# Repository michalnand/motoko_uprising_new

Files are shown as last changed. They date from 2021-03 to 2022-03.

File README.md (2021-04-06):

# motoko uprising new
motoko uprising line following robot,

**highlights**
- cpu stm32f7, 216MHz ARM Cortex M7
- DRV8834, TI motor driver
- 8x phototransistor + white led as line sensor
- IR leds for obstacle detection
- 2x pololu motors HP, 1:30 with encoder
- expansion : camera, laser sensor

- custom operating system
- reccurent LSTM in controll loop
- total 3 other PIDs used

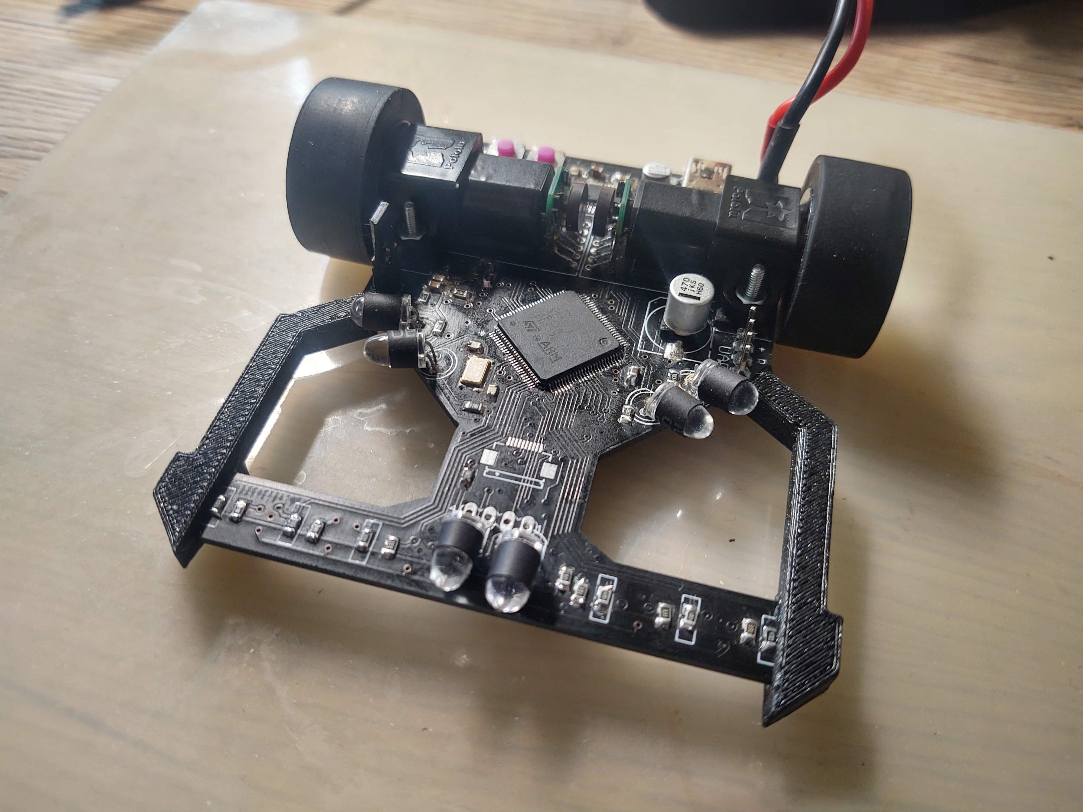
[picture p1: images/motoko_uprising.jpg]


# structure
 
 * src
    * firmware - robot main firmware
    * robot_debug_py - debug application
    * AI gym env for reinforcement learning [gym-line_follower](src/gym-line_follower/)
    * TODO rl_line_follower [rl_line_follower](src/rl_line_follower/)

* hardware 
    * eagle files [hardware](hardware/)
    * gerber outputs [files](hardware/CAMOutputs/)
    * stl for 3D printed parts [files](hardware/mechanical/)

# supervised learning for line position prediction

**key points**
* **input**  is time series sequence from 8 line sensors
* **output** is classification into three classes (left, straight, righ)
* RNN GRU with 64 units used, and linear layer with 3 neurons

* confusion matrix result for **float32**
```bash
accuracy   = 89.037 [%]
hit_count  = 116703
miss_count = 14369

class_accuracy = 90.952%   90.474%   84.811%   

confusion_matrix = 
       28326        1376           8
        2817       57907        5448
           0        4720       30470
```

* confusion matrix result for **int8** quantization

```bash
testing result
accuracy   = 87.792 [%]
hit_count  = 115071
miss_count = 16001

class_accuracy = 79.176%   91.345%   87.918%   

confusion_matrix = 
       22858        3566           0
        6011       62800        4041
           0        2383       29413
```

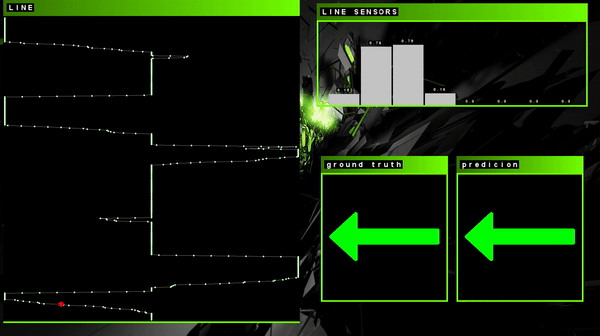
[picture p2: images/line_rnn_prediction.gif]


# reinforcement learning in Pybullet ENV

**key points**
* **state** is 256 last line positions, motors velocities, and line present flag

* PPO algorithm for continuous action space

* GRU model with three output heads (mean, variance, value)

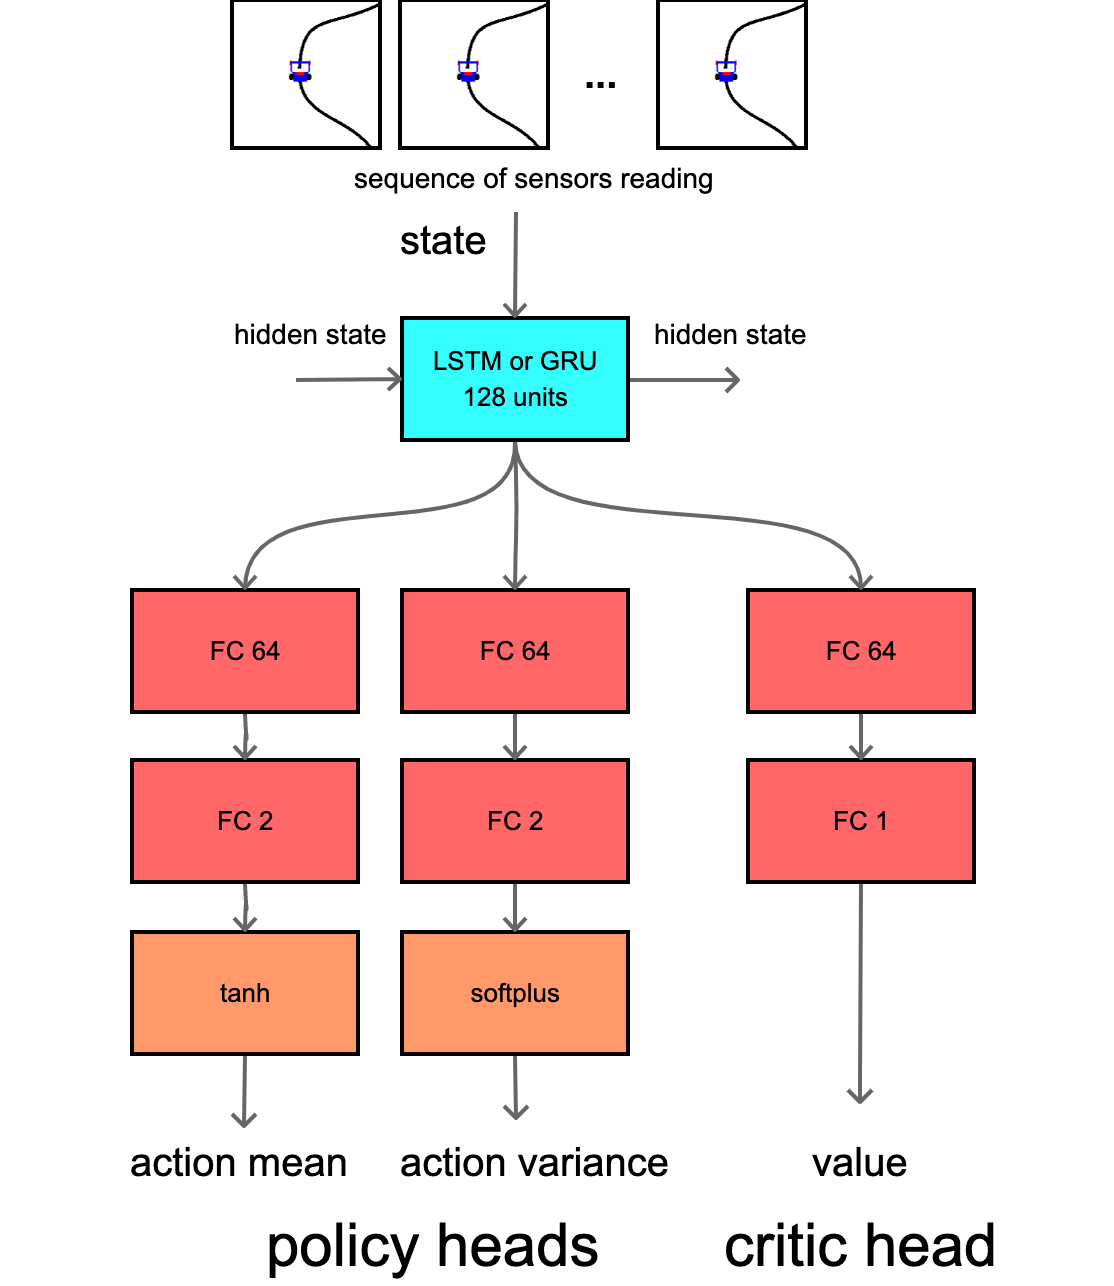
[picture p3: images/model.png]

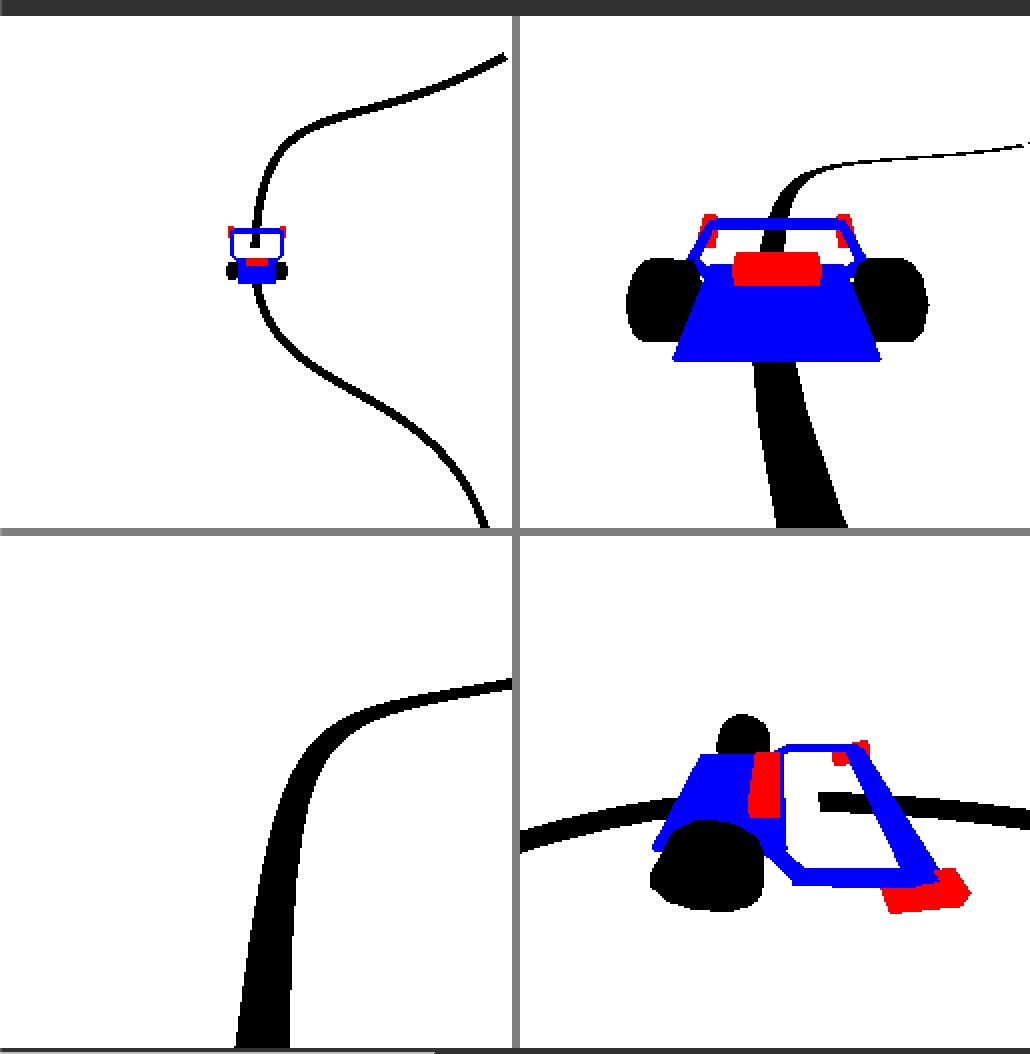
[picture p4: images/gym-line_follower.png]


# hardware

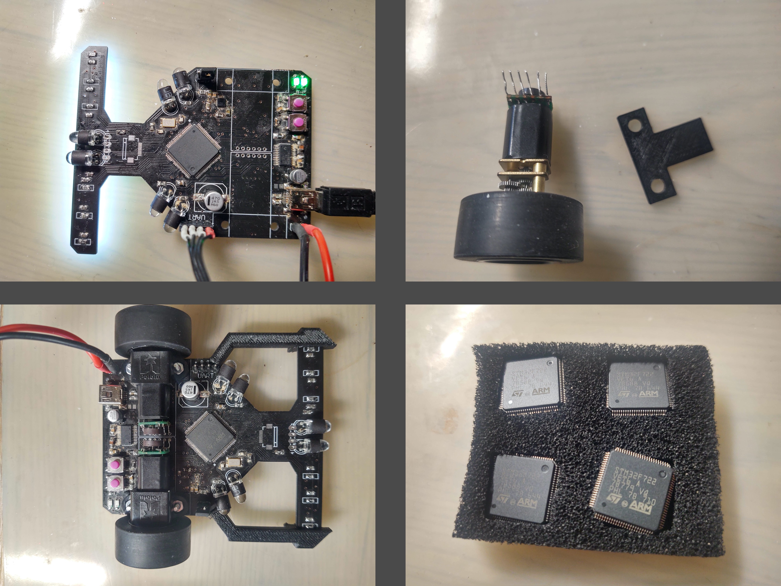
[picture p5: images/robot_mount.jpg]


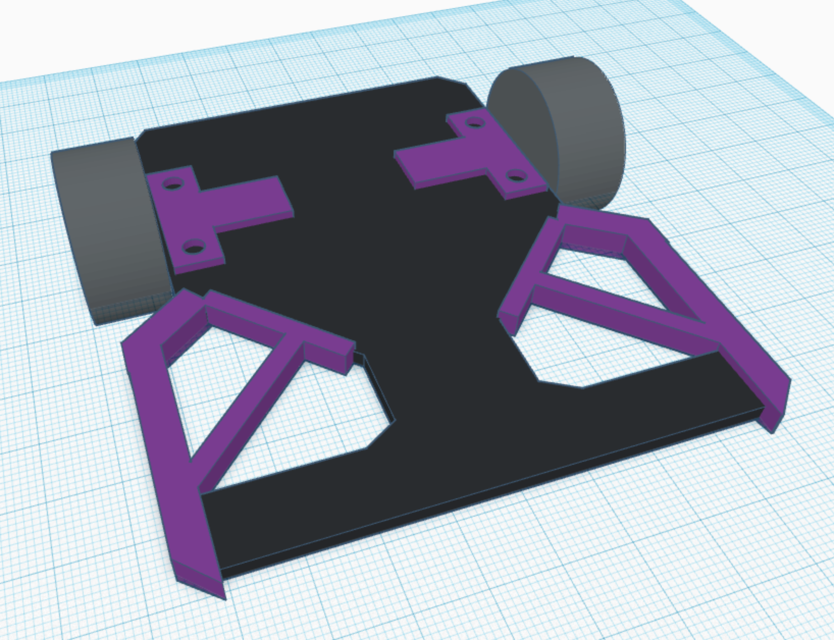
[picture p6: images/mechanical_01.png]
mechanical

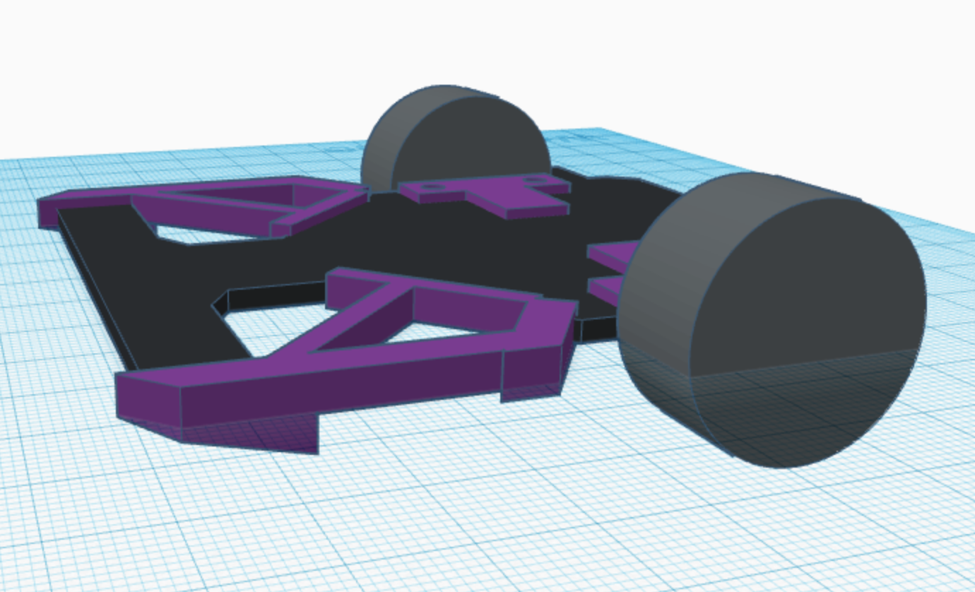
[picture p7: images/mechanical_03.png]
mechanical


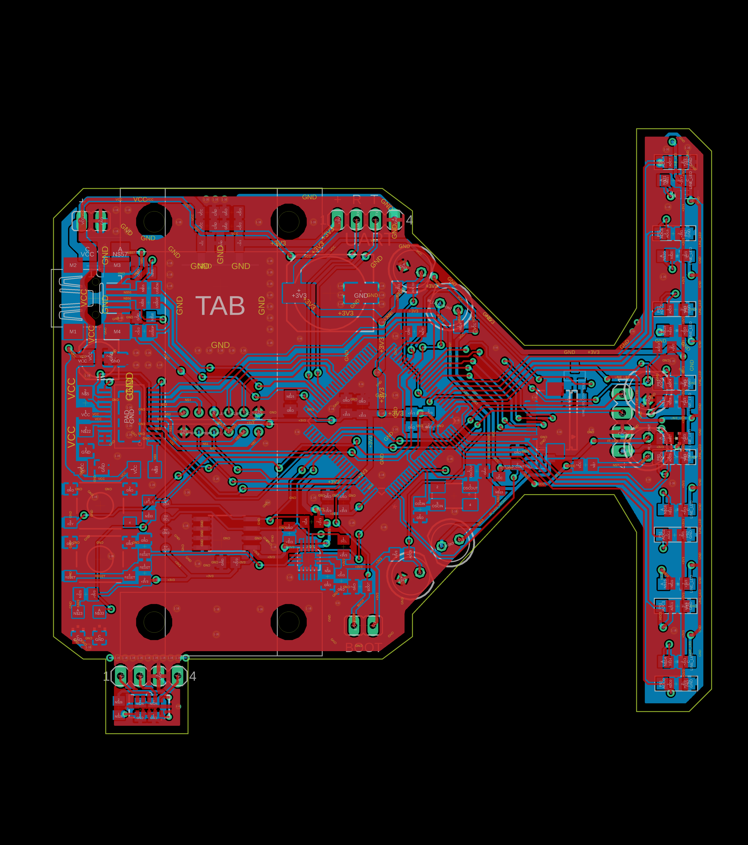
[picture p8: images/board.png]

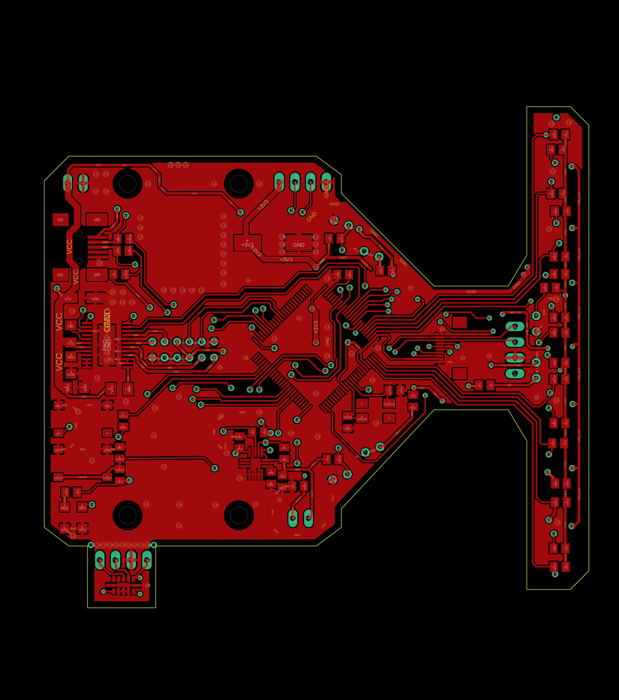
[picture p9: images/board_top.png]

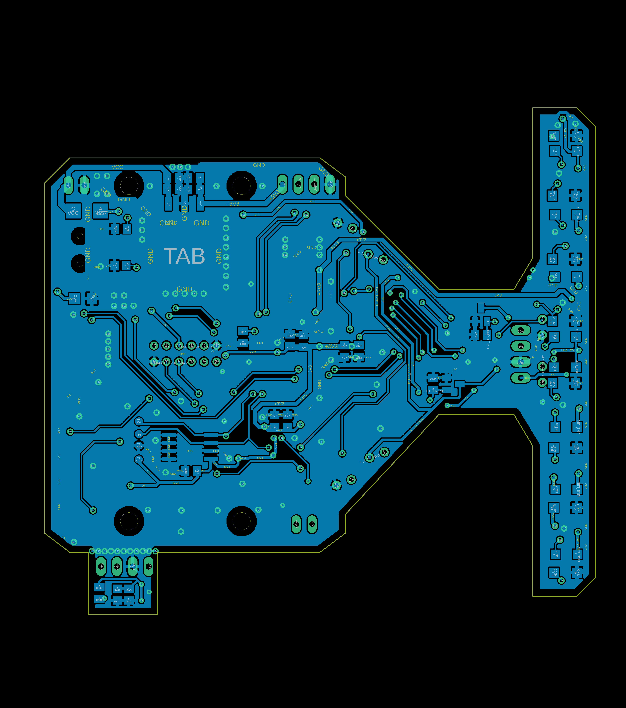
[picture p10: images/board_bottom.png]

hardware

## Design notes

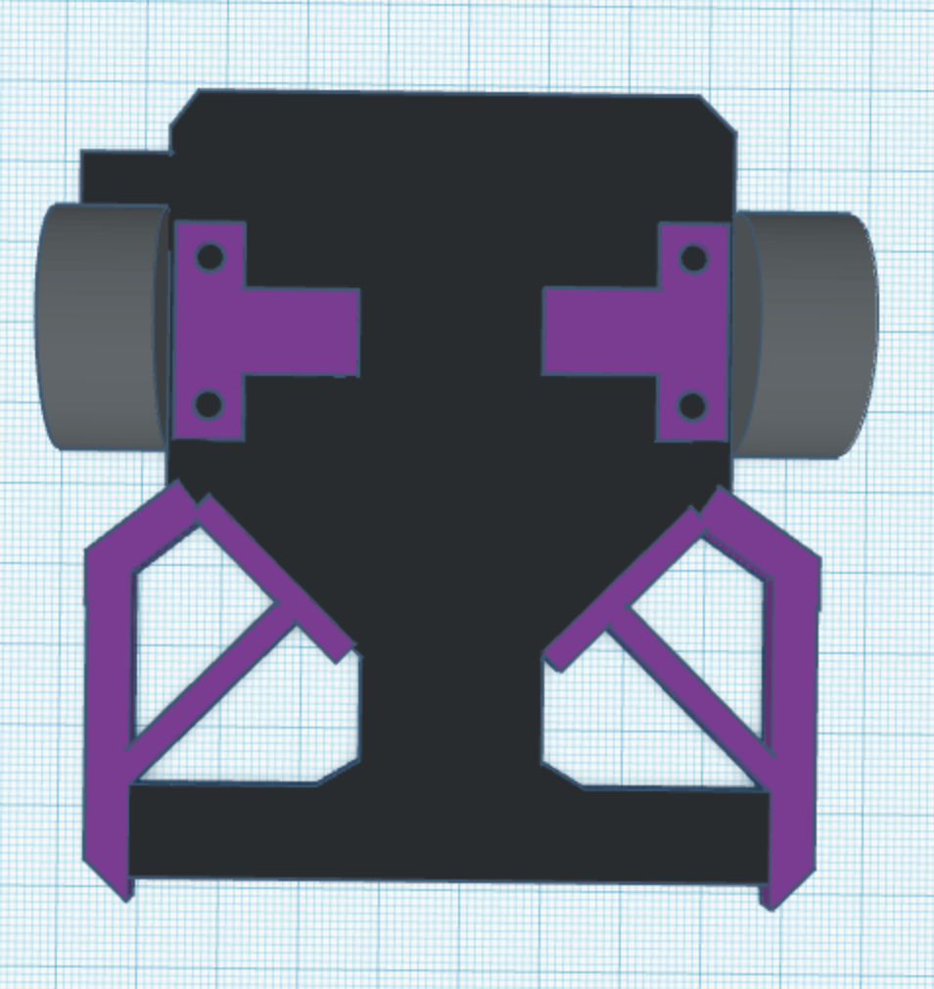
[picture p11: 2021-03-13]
images/mechanical_02.png

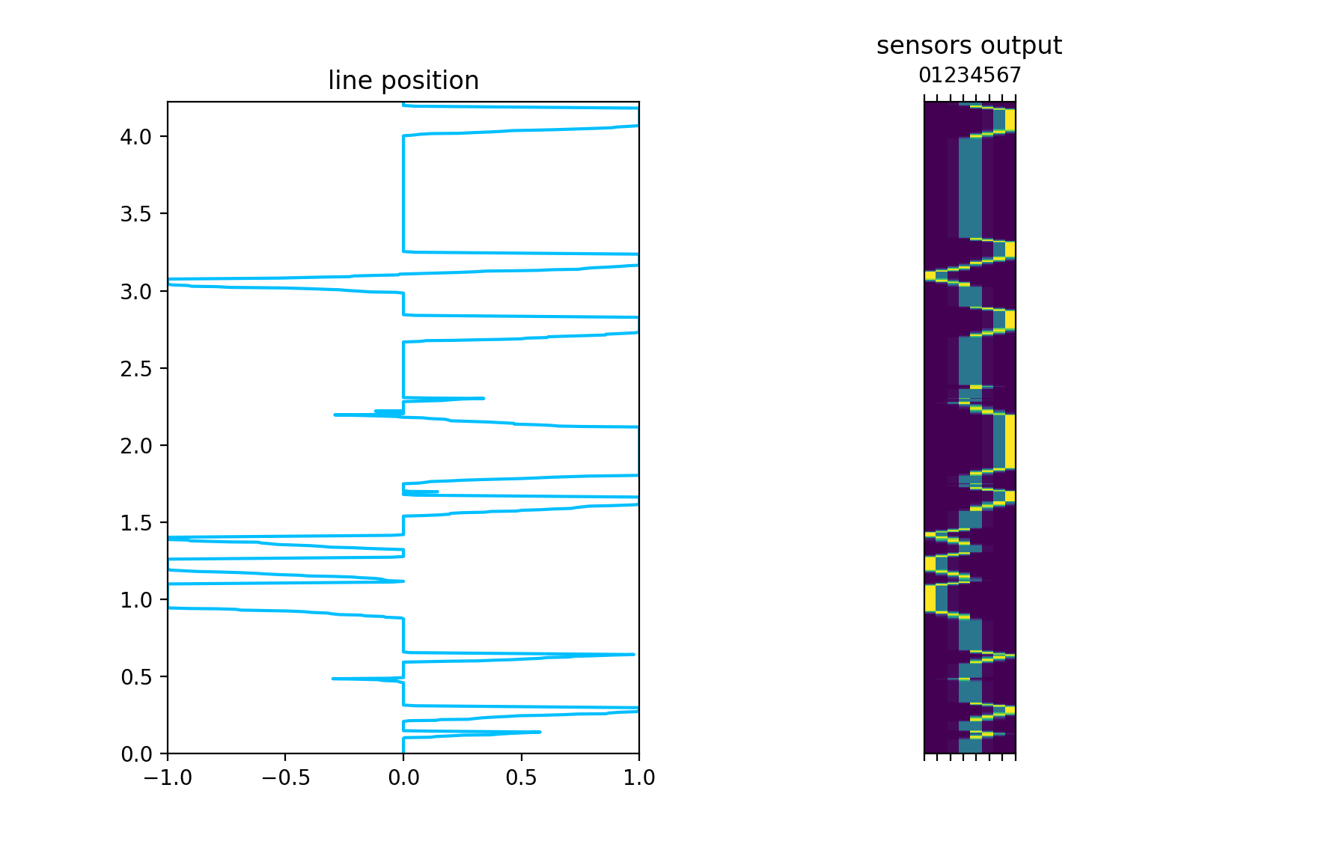
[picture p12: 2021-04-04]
images/line_follower_dataset.png

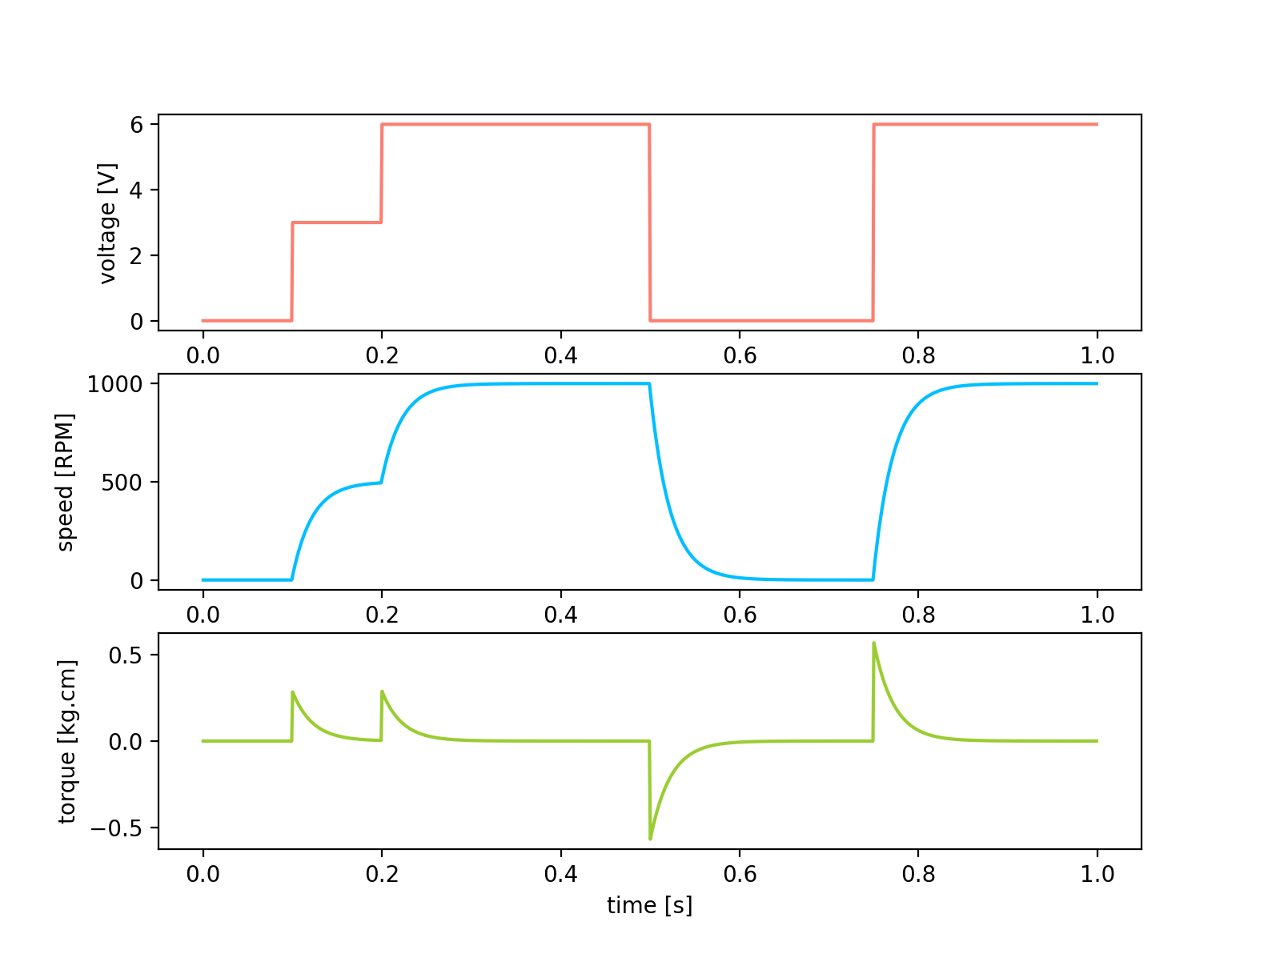
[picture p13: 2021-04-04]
images/motor_model.png

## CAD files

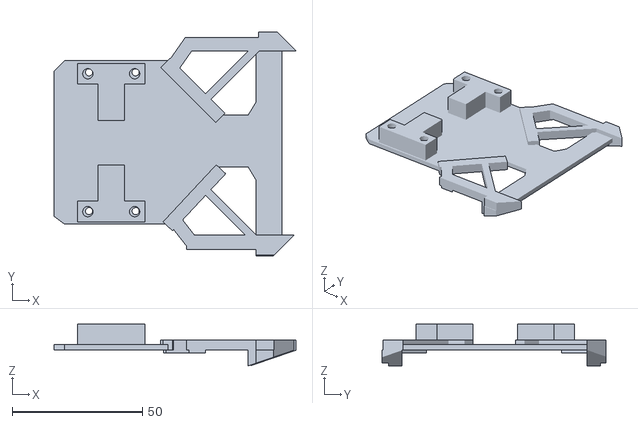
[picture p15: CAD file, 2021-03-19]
hardware/mechanical/model.stl
93.0 x 86.0 x 16.0

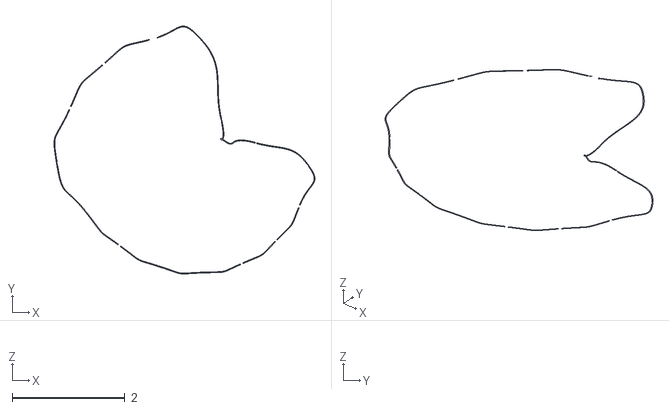
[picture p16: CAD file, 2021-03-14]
src/gym-line_follower/gym_line_follower/envs/models/lines/55.obj
4.62 x 4.39 x 0

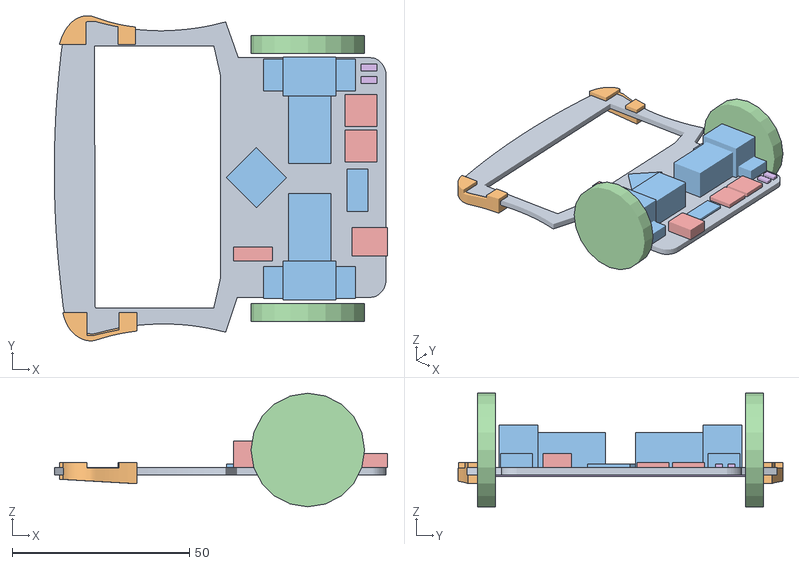
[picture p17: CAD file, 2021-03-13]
src/robot_debug_py/resources/robot_model/model.obj
93.9 x 91.6 x 32.0

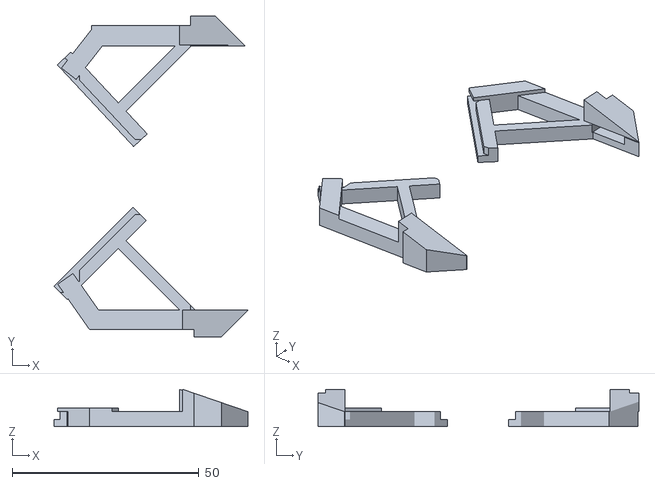
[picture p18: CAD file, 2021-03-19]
hardware/mechanical/forward_chassis.stl
52.0 x 86.0 x 10.0

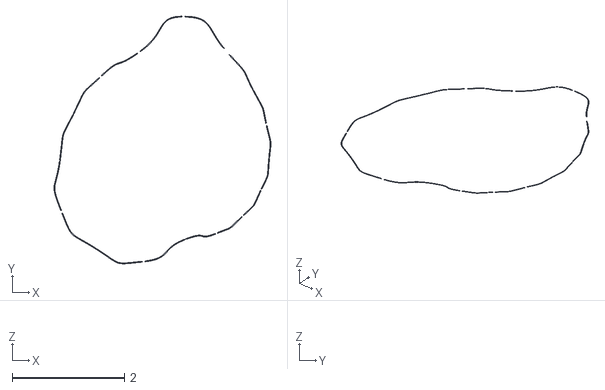
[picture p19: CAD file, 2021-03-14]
src/gym-line_follower/gym_line_follower/envs/models/lines/44.obj
3.86 x 4.40 x 0

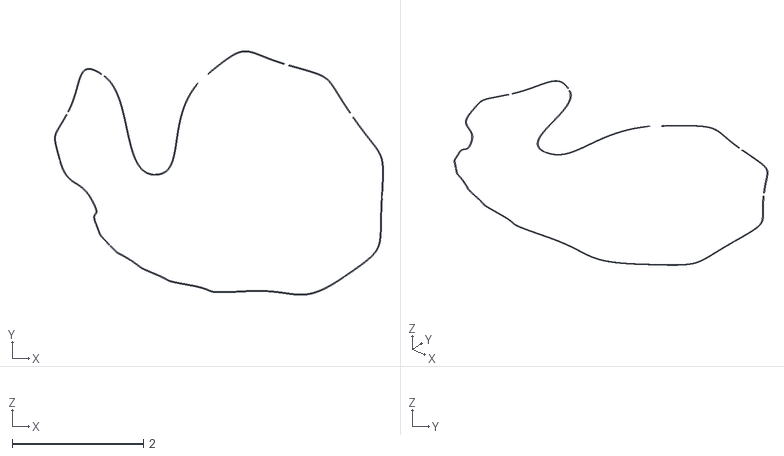
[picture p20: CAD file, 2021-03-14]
src/gym-line_follower/gym_line_follower/envs/models/lines/34.obj
5.02 x 3.73 x 0

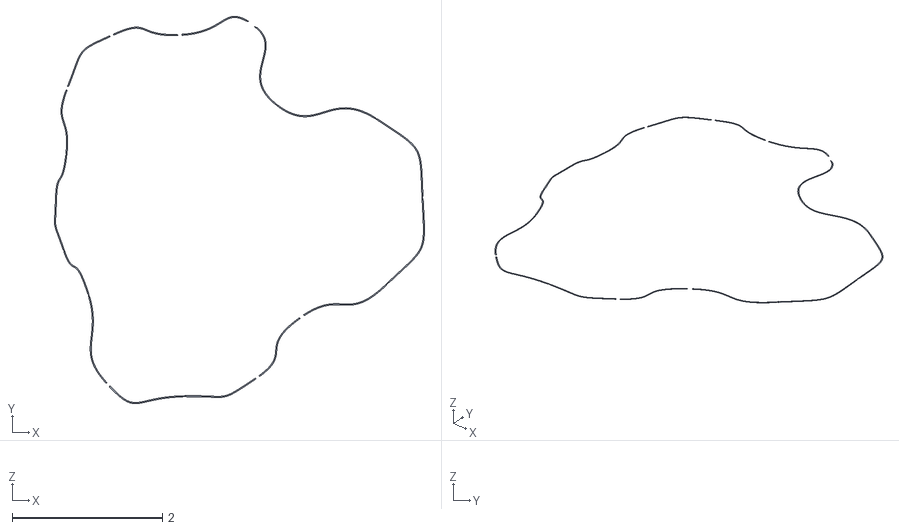
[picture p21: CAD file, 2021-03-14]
src/gym-line_follower/gym_line_follower/envs/models/lines/1.obj
4.92 x 5.15 x 0

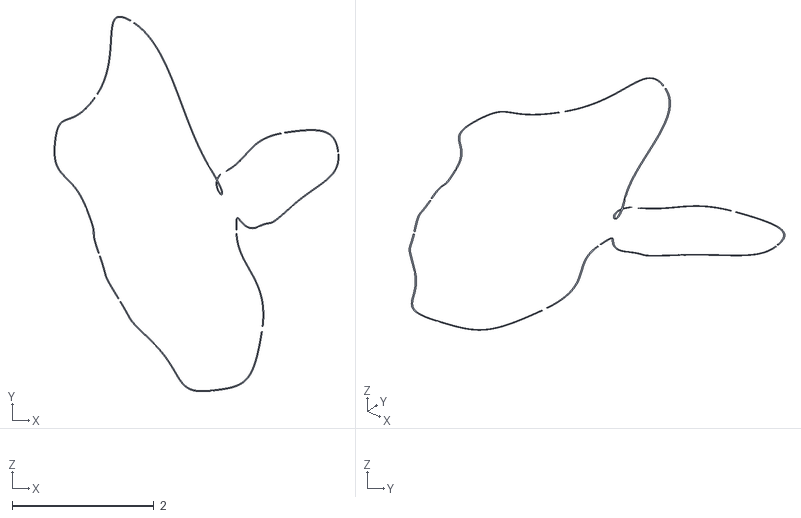
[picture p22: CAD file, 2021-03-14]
src/gym-line_follower/gym_line_follower/envs/models/lines/13.obj
4.02 x 5.29 x 0

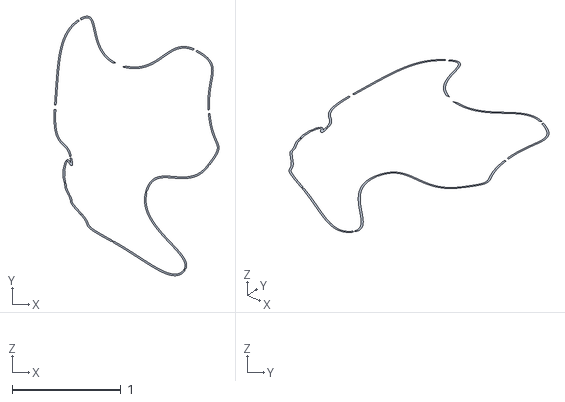
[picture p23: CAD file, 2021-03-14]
src/gym-line_follower/gym_line_follower/envs/models/lines/63.obj
1.52 x 2.39 x 0

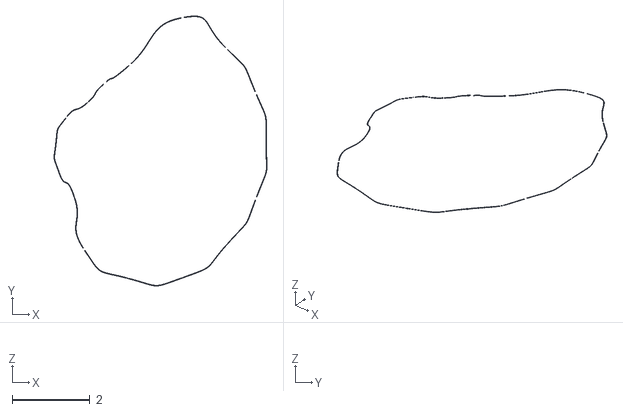
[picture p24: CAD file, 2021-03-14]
src/gym-line_follower/gym_line_follower/envs/models/lines/26.obj
5.49 x 6.95 x 0

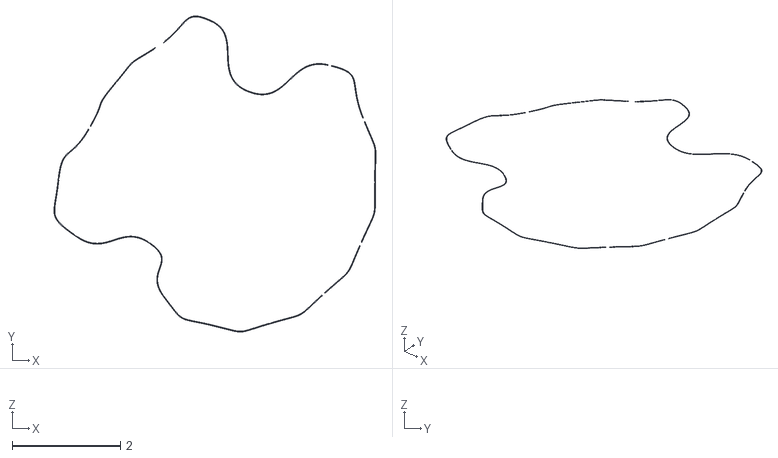
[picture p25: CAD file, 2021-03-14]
src/gym-line_follower/gym_line_follower/envs/models/lines/14.obj
5.95 x 5.84 x 0

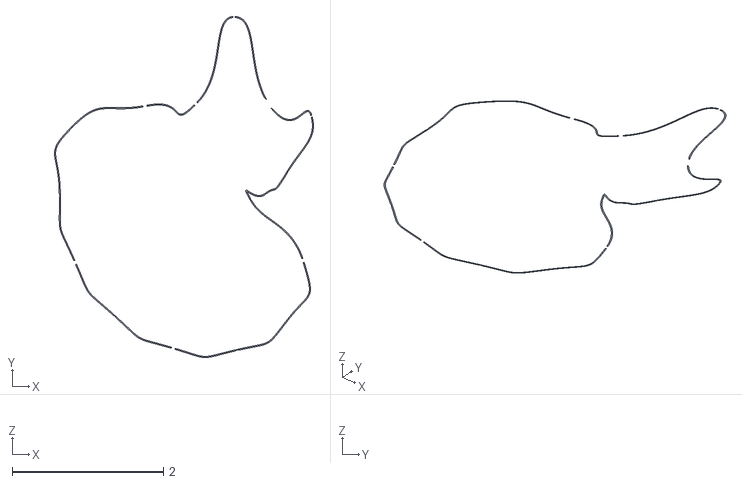
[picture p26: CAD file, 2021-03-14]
src/gym-line_follower/gym_line_follower/envs/models/lines/17.obj
3.43 x 4.51 x 0

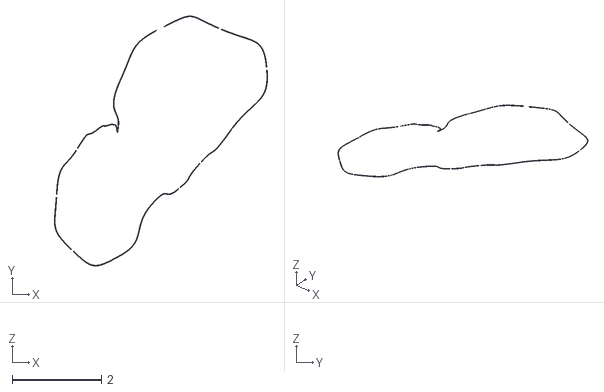
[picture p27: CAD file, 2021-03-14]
src/gym-line_follower/gym_line_follower/envs/models/lines/29.obj
4.77 x 5.59 x 0

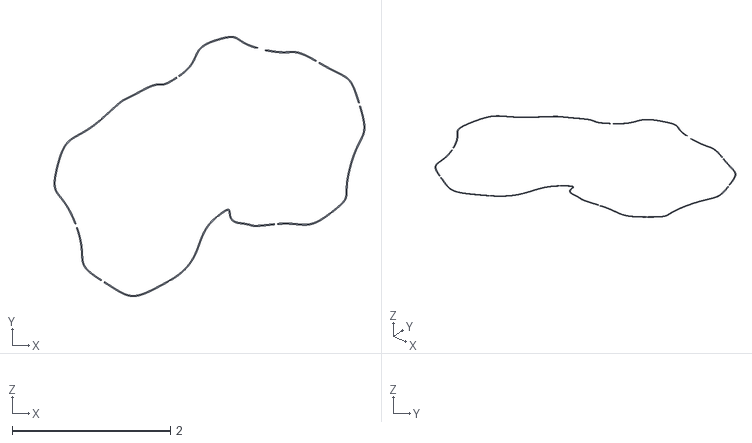
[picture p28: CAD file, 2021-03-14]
src/gym-line_follower/gym_line_follower/envs/models/lines/60.obj
3.93 x 3.29 x 0

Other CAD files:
src/gym-line_follower/gym_line_follower/envs/models/lines/30.obj
src/gym-line_follower/gym_line_follower/envs/models/lines/15.obj
src/gym-line_follower/gym_line_follower/envs/models/lines/31.obj
src/gym-line_follower/gym_line_follower/envs/models/lines/7.obj
src/gym-line_follower/gym_line_follower/envs/models/lines/0.obj
src/gym-line_follower/gym_line_follower/envs/models/lines/10.obj
src/gym-line_follower/gym_line_follower/envs/models/lines/11.obj
src/gym-line_follower/gym_line_follower/envs/models/lines/12.obj
src/gym-line_follower/gym_line_follower/envs/models/lines/16.obj
src/gym-line_follower/gym_line_follower/envs/models/lines/18.obj
src/gym-line_follower/gym_line_follower/envs/models/lines/19.obj
src/gym-line_follower/gym_line_follower/envs/models/lines/2.obj
src/gym-line_follower/gym_line_follower/envs/models/lines/20.obj
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

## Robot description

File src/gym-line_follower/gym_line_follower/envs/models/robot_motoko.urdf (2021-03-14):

<?xml version="1.0"?>
<robot name="line_follower">

    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


  
  
	<link name="main_board_0">
    	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
  
   		  <inertial>
            <mass value="0.053"/>
            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
        </inertial>
	</link>


	<link name="main_board_1">
    	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
  
   		<inertial>
            <mass value="0.02"/>
            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
        </inertial>
	</link>



    <link name="main_board_left_a">
    	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
  
   		<inertial>
            <mass value="0.0"/>
            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
        </inertial>
	</link>



	<link name="main_board_left_b">
    	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
  
   		<inertial>
            <mass value="0.0"/>
            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
        </inertial>
	</link>




    <link name="main_board_right_a">
    	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
  
   		<inertial>
            <mass value="0.0"/>
            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
        </inertial>
	</link>



	<link name="main_board_right_b">
    	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
  
   		<inertial>
            <mass value="0.0"/>
            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
        </inertial>
	</link>


  <link name="front_left">
    	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

        <inertial>
            <mass value="0.0005"/>
            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
        </inertial>
	</link>


	<link name="front_right">
    	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

        <inertial>
            <mass value="0.0005"/>
            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
        </inertial>
	</link>


  <link name="accu">
    	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
  
   		<inertial>
            <mass value="0.01"/>
            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
        </inertial>
	</link>



	<link name="left_wheel">
        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


        <inertial>
            <mass value="0.01"/>
            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
        </inertial>
    </link>

    

	<link name="right_wheel">
        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

        <inertial>
            <mass value="0.01"/>
            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
        </inertial>
    </link>








	<joint name="main_board_0_left_wheel" type="continuous">
    <parent link="main_board_0"/>
    <child link="left_wheel"/>
    <origin rpy="-1.5708 0.0 0" xyz="0.0 0.041 0.0025"/>
    <axis xyz="0 0 1"/>
  </joint>


  <joint name="main_board_0_right_wheel" type="continuous">
    <parent link="main_board_0"/>
    <child link="right_wheel"/>
    <origin rpy="1.5708 0.0 0" xyz="0.0 -0.041 0.0025"/>
    <axis xyz="0 0 -1"/>
  </joint>




	<joint name="main_board_0_main_board_1" type="fixed">
		<parent link="main_board_0"/>
		<child link="main_board_1"/>
    <origin rpy="0 0 0" xyz="0.067 0.0 0.0"/>
 	</joint>


<joint name="main_board_1_front_0" type="fixed">
		<parent link="main_board_1"/>
		<child link="front_left"/>
    <origin rpy="0 -0.3 0" xyz="0.0 0.044 -0.005"/>
 	</joint>

	<joint name="main_board_1_front_1" type="fixed">
		<parent link="main_board_1"/>
		<child link="front_right"/>
    <origin rpy="0 -0.3 0" xyz="0.0 -0.044 -0.005"/>
 	</joint>





  <joint name="main_board_0_accu" type="fixed">
		<parent link="main_board_0"/>
		<child link="accu"/>
    <origin rpy="0.0 0 0" xyz="0.015 0.0 0.005"/>
 	</joint>


  <joint name="main_board_0_main_board_left_a" type="fixed">
		<parent link="main_board_0"/>
		<child link="main_board_left_a"/>
    <origin rpy="0 0 0" xyz="0.045 0.042 0.0"/>
 	</joint>

  <joint name="main_board_0_main_board_left_b" type="fixed">
		<parent link="main_board_0"/>
		<child link="main_board_left_b"/>
    <origin rpy="0 0 0.785" xyz="0.021 0.035 0.0"/>
 	</joint>

  <joint name="main_board_0_main_board_right_a" type="fixed">
		<parent link="main_board_0"/>
		<child link="main_board_right_a"/>
    <origin rpy="0 0 0" xyz="0.045 -0.042 0.0"/>
 	</joint>

  <joint name="main_board_0_main_board_right_b" type="fixed">
		<parent link="main_board_0"/>
		<child link="main_board_right_b"/>
    <origin rpy="0 0 -0.785" xyz="0.021 -0.035 0.0"/>
 	</joint>

</robot>

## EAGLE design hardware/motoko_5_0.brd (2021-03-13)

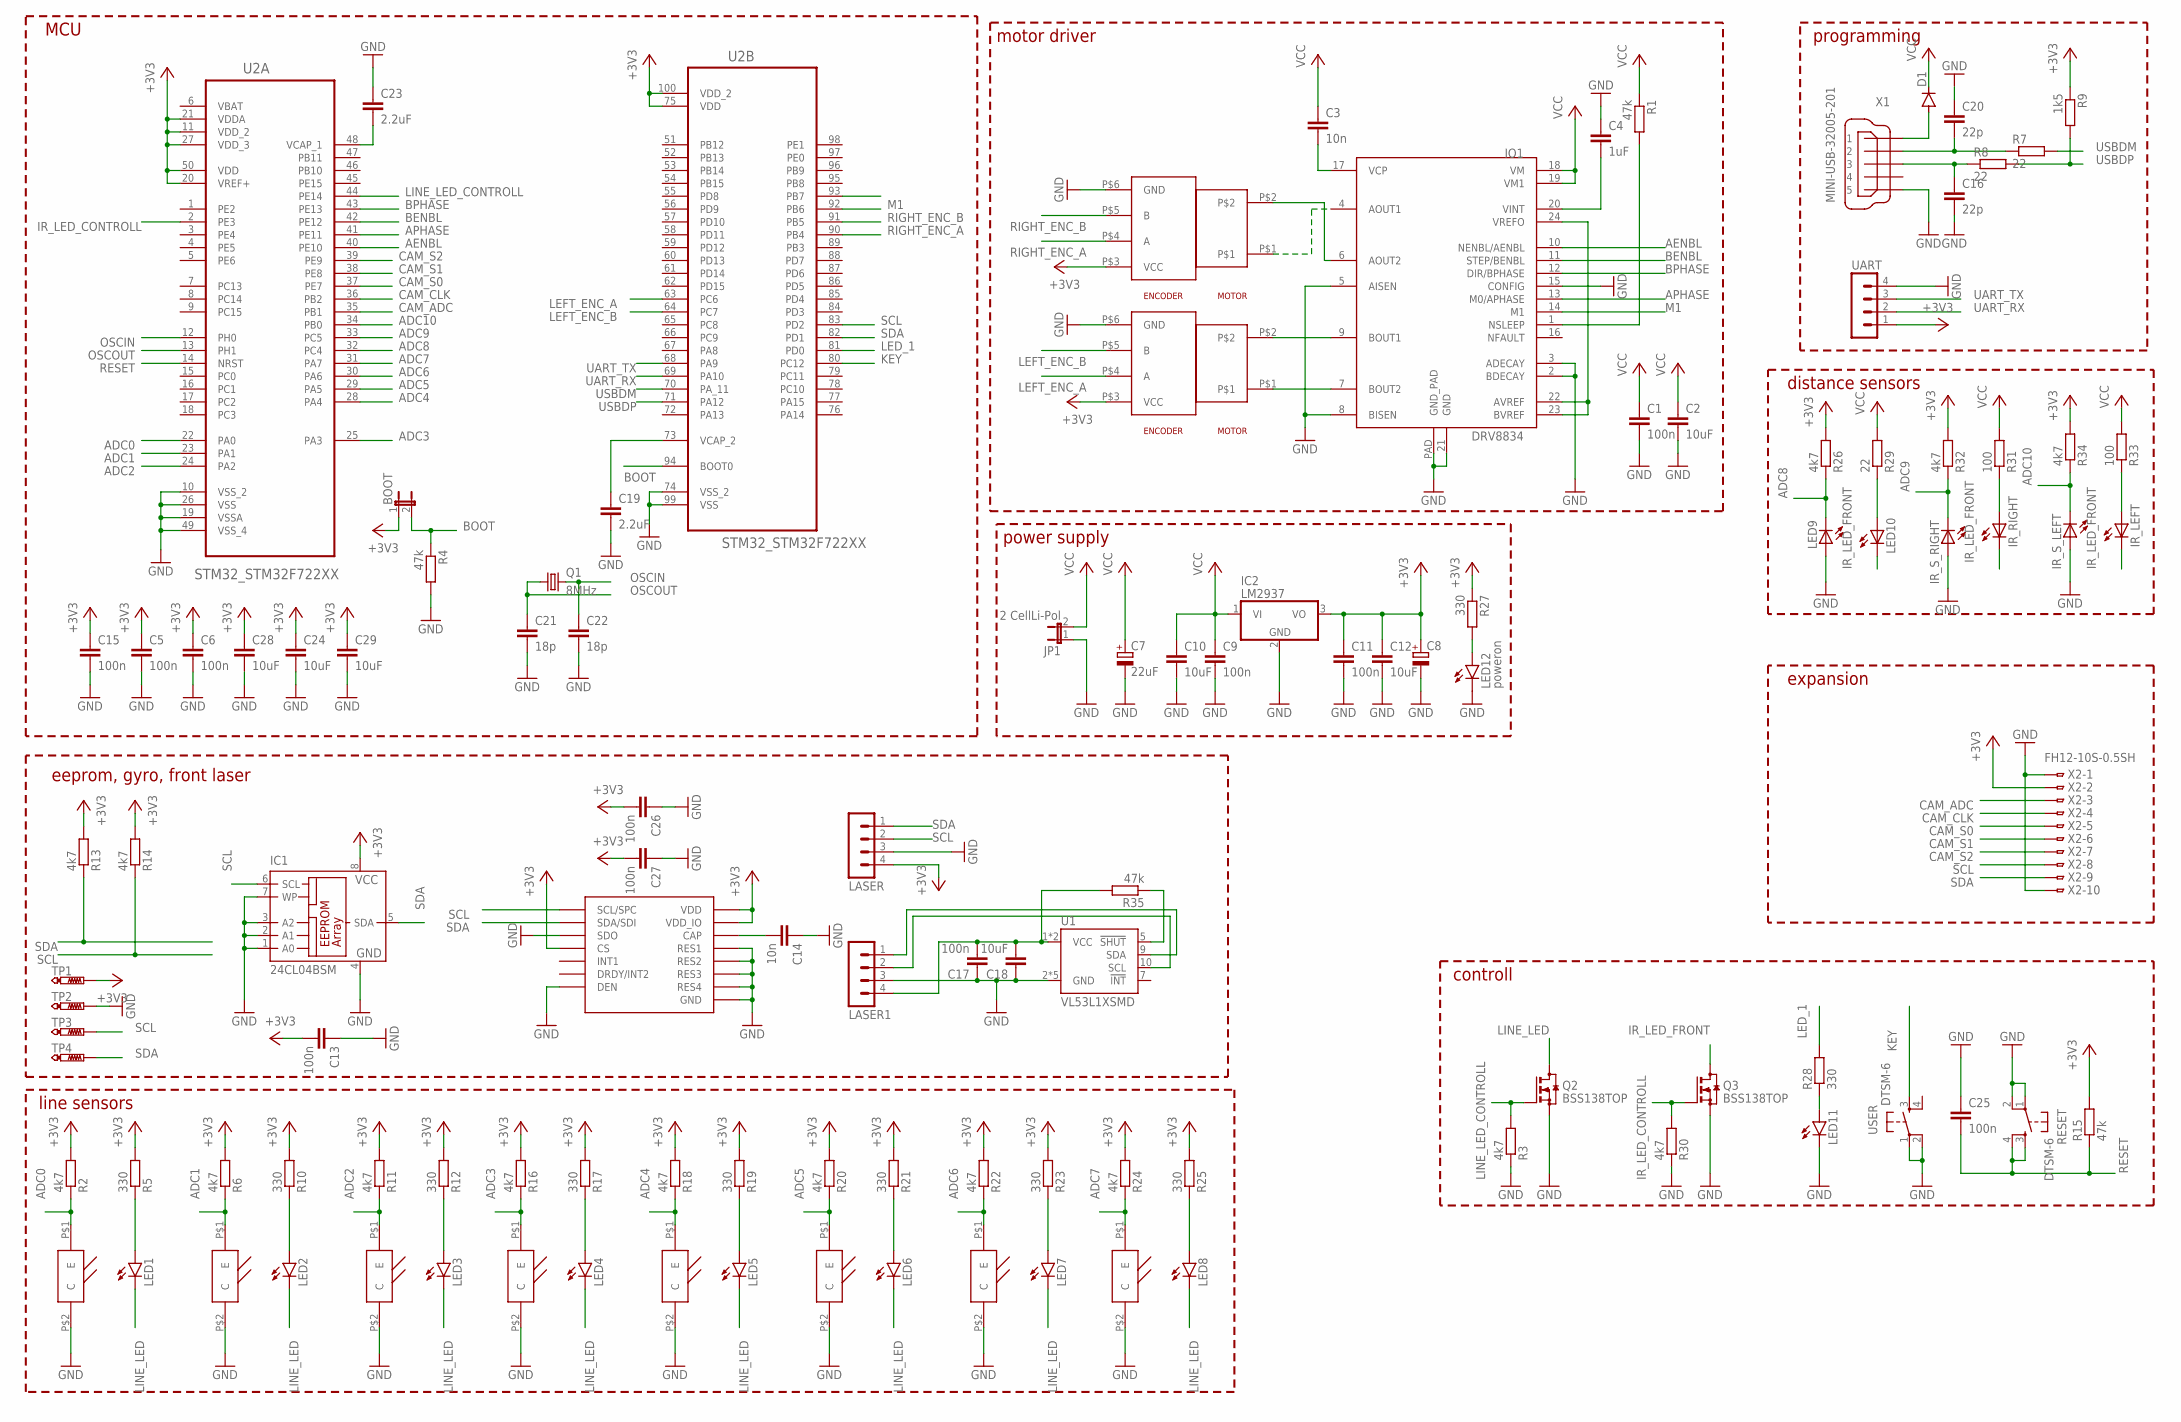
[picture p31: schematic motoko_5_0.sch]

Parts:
BOOT: JP1E; JP1
C1: 100n; C1206
C2: 10uF; C1206
C3: 10n; C1206
C4: 1uF; C1206
C5, C6, C9, C11, C13, C15, C17, C25, C26, C27: 100n; C0805
C7: 22uF; 153CLV-0505
C8: CPOL-EU140CLH-1010; 140CLH-1010
C10, C12, C18, C24, C28, C29: 10uF; C0805
C14: 10n; C0805
C16, C20: 22p; C0805
C19, C23: 2.2uF; C0805
C21, C22: 18p; C0805
D1: DIODE-SMB; SMB
IC1: 24CL04BSM; SO-08M
IC2: LM2937; TO263-3
IO1: DRV8834; DRV8834_PCK
IR_LEFT: LED5MM
IR_RIGHT: LED5MM
IR_S_LEFT: LED5MM
IR_S_RIGHT: LED5MM
JP1: 2 CellLi-Pol; JP1
LASER, LASER1: MA04-1
LED1, LED2, LED3, LED4, LED5, LED6, LED7, LED8, LED11: LEDCHIPLED_1206; CHIPLED_1206
LED9, LED10: LED5MM
LED12: poweron; CHIPLED_1206
LSM6DS0: ST_L3GD20H; ST_LGA16L
Q1: 8MHz; CTS406
Q2, Q3: BSS138TOP; SOT23
R1: 47k; M1206
R2, R3, R6, R11, R13, R14, R16, R18, R20, R22, R24, R26, R30, R32, R34: 4k7; M0805
R4, R15, R35: 47k; M0805
R5, R10, R12, R17, R19, R21, R23, R25, R27, R28: 330; M0805
R7, R8, R29: 22; M0805
R9: 1k5; M0805
R31, R33: 100; M0805
RESET: DTSM-6
TP1, TP2, TP3, TP4: PTR1B1,27; B1,27
U1: VL53L1XSMD; VL53L1X
U2: STM32_STM32F722XX; STM32_QFP50P1600X1600X160-100N
U$3, U$4, U$5, U$6, U$7, U$8, U$9, U$10: SFH3710
U$11, U$12: POLOLU_GEAR_MOTORPOLO; POLOLU_GEAR_MOTOR
UART: MA04-1
USER: DTSM-6
X1: MINI-USB-32005-201; 32005-201
X2: FH12-10S-0.5SH

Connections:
+3V3: BOOT.1, C5.1, C6.1, C8.+, C11.1, C12.1, C13.2, C15.1, C24.1, C26.2, C27.2, C28.1, C29.1, IC1.8 (VCC), IC2.3 (VO), LASER.4, LSM6DS0.P$1 (VDD_IO), LSM6DS0.P$5 (CS), LSM6DS0.P$16 (VDD), R2.2, R5.2, R6.2, R9.1, R10.2, R11.2, R12.2, R13.2, R14.2, R15.2, R16.2, R17.2, R18.2, R19.2, R20.2, R21.2, R22.2, R23.2, R24.2, R25.2, R26.2, R27.1, R32.2, R34.2, TP1.TP, U2.11 (VDD_2), U2.20 (VREF+), U2.21 (VDDA), U2.27 (VDD_3), U2.50 (VDD), U2.75 (VDD), U2.100 (VDD_2), U$11.P$3 (VCC), U$12.P$3 (VCC), UART.1, X2.2
ADC0: R2.1, U2.22 (PA0), U$3.P$1 (E)
ADC1: R6.1, U2.23 (PA1), U$4.P$1 (E)
ADC2: R11.1, U2.24 (PA2), U$5.P$1 (E)
ADC3: R16.1, U2.25 (PA3), U$6.P$1 (E)
ADC4: R18.1, U2.28 (PA4), U$7.P$1 (E)
ADC5: R20.1, U2.29 (PA5), U$8.P$1 (E)
ADC6: R22.1, U2.30 (PA6), U$9.P$1 (E)
ADC7: R24.1, U2.31 (PA7), U$10.P$1 (E)
ADC8: LED9.K (C), R26.1, U2.32 (PC4)
ADC9: IR_S_RIGHT.K (C), R32.1, U2.33 (PC5)
ADC10: IR_S_LEFT.K (C), R34.1, U2.34 (PB0)
AENBL: IO1.10 (NENBL/AENBL), U2.40 (PE10)
APHASE: IO1.13 (M0/APHASE), U2.41 (PE11)
BENBL: IO1.11 (STEP/BENBL), U2.42 (PE12)
BOOT: BOOT.2, R4.1, U2.94 (BOOT0)
BPHASE: IO1.12 (DIR/BPHASE), U2.43 (PE13)
CAM_ADC: U2.35 (PB1), X2.3
CAM_CLK: U2.36 (PB2), X2.4
CAM_S0: U2.37 (PE7), X2.5
CAM_S1: U2.38 (PE8), X2.6
CAM_S2: U2.39 (PE9), X2.7
GND: C1.2, C2.2, C4.1, C5.2, C6.2, C7.-, C8.-, C9.2, C10.2, C11.2, C12.2, C13.1, C14.1, C15.2, C16.2, C17.1, C18.1, C19.2, C20.1, C21.2, C22.2, C23.1, C24.2, C25.1, C26.1, C27.1, C28.2, C29.2, IC1.1 (A0), IC1.2 (A1), IC1.3 (A2), IC1.4 (GND), IC1.7 (WP), IC2.2 (GND), IO1.2 (BDECAY), IO1.3 (ADECAY), IO1.5 (AISEN), IO1.8 (BISEN), IO1.15 (CONFIG), IO1.21 (GND), IO1.PAD (GND_PAD), IR_S_LEFT.A, IR_S_RIGHT.A, JP1.1, LASER.3, LASER1.3, LED9.A, LED11.C, LED12.C, LSM6DS0.P$4 (SDO), LSM6DS0.P$8 (DEN), LSM6DS0.P$9 (RES1), LSM6DS0.P$10 (RES2), LSM6DS0.P$11 (RES3), LSM6DS0.P$12 (GND), LSM6DS0.P$13 (GND), LSM6DS0.P$15 (RES4), Q2.2 (S), Q3.2 (S), R3.1, R4.2, R30.1, RESET.1, RESET.2, TP2.TP, U1.2 (GND), U1.3 (GND), U1.4 (GND), U1.6 (GND), U1.12 (GND), U2.10 (VSS_2), U2.19 (VSSA), U2.26 (VSS), U2.49 (VSS_4), U2.74 (VSS_2), U2.99 (VSS), U$3.P$2 (C), U$4.P$2 (C), U$5.P$2 (C), U$6.P$2 (C), U$7.P$2 (C), U$8.P$2 (C), U$9.P$2 (C), U$10.P$2 (C), U$11.P$6 (GND), U$12.P$6 (GND), UART.4, USER.1, USER.2, X1.5, X2.1, X2.10
IR_LED_CONTROLL: Q3.1 (G), R30.2, U2.2 (PE3)
IR_LED_FRONT: IR_LEFT.K (C), IR_RIGHT.K (C), LED10.K (C), Q3.3 (D)
KEY: U2.80 (PC12), USER.3
LED_1: R28.2, U2.81 (PD0)
LEFT_ENC_A: U2.63 (PC6), U$11.P$4 (A)
LEFT_ENC_B: U2.64 (PC7), U$11.P$5 (B)
LINE_LED: LED1.C, LED2.C, LED3.C, LED4.C, LED5.C, LED6.C, LED7.C, LED8.C, Q2.3 (D)
LINE_LED_CONTROLL: Q2.1 (G), R3.2, U2.44 (PE14)
M1: IO1.14 (M1), U2.92 (PB6)
unnamed: IO1.6 (AOUT2), U$12.P$2
unnamed: IO1.4 (AOUT1), U$12.P$1
unnamed: IO1.7 (BOUT2), U$11.P$1
unnamed: IO1.9 (BOUT1), U$11.P$2
unnamed: C3.2, IO1.17 (VCP)
unnamed: C14.2, LSM6DS0.P$14 (CAP)
unnamed: LED10.A, R29.1
unnamed: IO1.22 (AVREF), IO1.23 (BVREF), IO1.24 (VREFO)
unnamed: IO1.1 (NSLEEP), R1.2
unnamed: IR_LEFT.A, R33.1
unnamed: LED1.A, R5.1
unnamed: LED2.A, R10.1
unnamed: LED3.A, R12.1
unnamed: LED4.A, R17.1
unnamed: LED5.A, R19.1
unnamed: LED6.A, R21.1
unnamed: LED7.A, R23.1
unnamed: LED8.A, R25.1
unnamed: C4.2, IO1.20 (VINT)
unnamed: LED12.A, R27.2
unnamed: IR_RIGHT.A, R31.1
unnamed: C19.1, U2.73 (VCAP_2)
unnamed: C17.2, C18.2, LASER1.4, R35.2, U1.1 (VCC), U1.11 (VCC)
unnamed: LASER1.1, U1.9 (SDA)
unnamed: LASER1.2, U1.10 (SCL)
unnamed: R35.1, U1.5 (!SHUT)
unnamed: C23.2, U2.48 (VCAP_1)
unnamed: LED11.A, R28.1
unnamed: C20.2, R7.1, X1.2
unnamed: C16.1, R8.1, X1.3
unnamed: D1.A, X1.1
OSCIN: C22.1, Q1.3 (2), U2.12 (PH0)
OSCOUT: C21.1, Q1.1, U2.13 (PH1)
RESET: C25.2, R15.1, RESET.3, RESET.4, U2.14 (NRST)
RIGHT_ENC_A: U2.90 (PB4), U$12.P$4 (A)
RIGHT_ENC_B: U2.91 (PB5), U$12.P$5 (B)
SCL: IC1.6 (SCL), LASER.2, LSM6DS0.P$2 (SCL/SPC), R14.1, TP3.TP, U2.83 (PD2), X2.8
SDA: IC1.5 (SDA), LASER.1, LSM6DS0.P$3 (SDA/SDI), R13.1, TP4.TP, U2.82 (PD1), X2.9
UART_RX: U2.69 (PA10), UART.2
UART_TX: U2.68 (PA9), UART.3
USBDM: R7.2, U2.70 (PA_11)
USBDP: R8.2, R9.2, U2.71 (PA12)
VBAT: U2.6 (VBAT)
VCC: C1.1, C2.1, C3.1, C7.+, C9.1, C10.1, D1.C, IC2.1 (VI), IO1.18 (VM), IO1.19 (VM1), JP1.2, R1.1, R29.2, R31.2, R33.2

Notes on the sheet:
power supply
line sensors
programming
MCU
motor driver
distance sensors
controll
eeprom, gyro, front laser
expansion

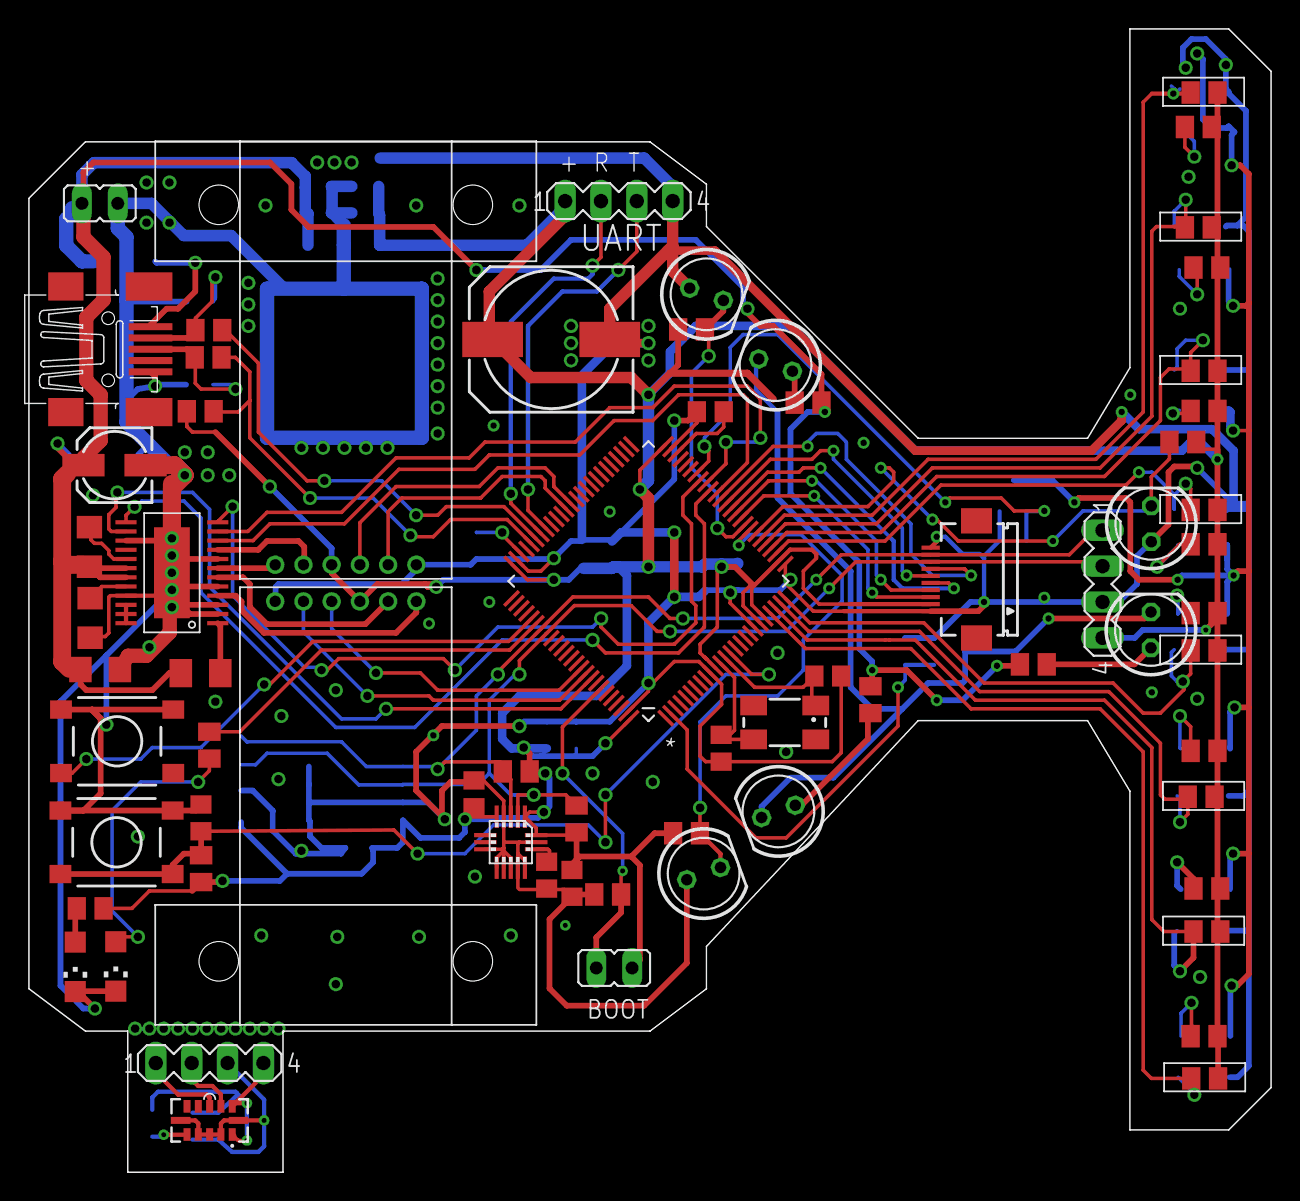
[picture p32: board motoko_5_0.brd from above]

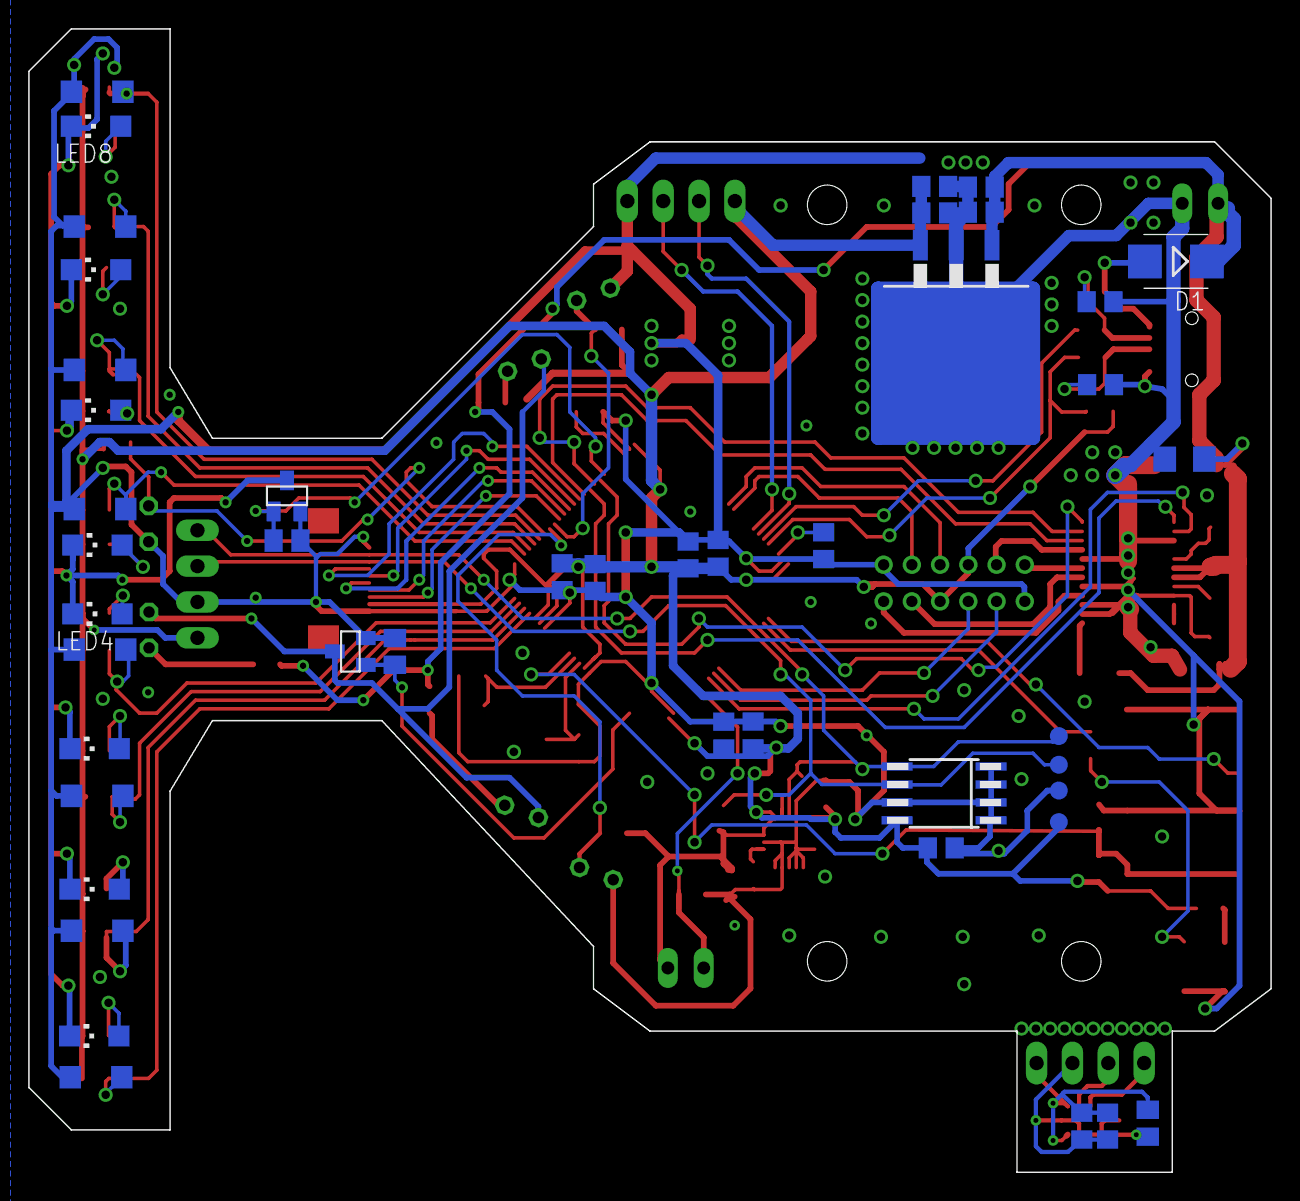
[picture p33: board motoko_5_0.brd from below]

Board: 2 copper layers, 88.0 x 81.0 mm, 113 parts (45 on the bottom side), 75 nets.

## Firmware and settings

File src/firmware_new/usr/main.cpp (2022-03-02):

#include "device.h"
#include <clock.h>
#include <gpio.h>
#include <low_level_drivers.h>

#include <motor_controll.h>

#include <fmath.h>

 
#define LED_GPIO        TGPIOD
#define LED_PIN         0

#define KEY_GPIO        TGPIOC
#define KEY_PIN         12
  

void speed_control()
{
  float speed_max      = 0.0;
  float dt             = 4;
  float t              = 0.0;
  float required_speed = 800.0;
 
  MotorControll motor_controll;
 
  motor_controll.init(0.0065, -0.0065 + 0.002, 0.02, 0.1); 

  motor_controll.left_set(required_speed);

  for (unsigned int i = 0; i < 100; i++)
  {
    float speed = encoder_driver.get_left_speed();
    terminal << t << " " << speed << "\n";
    

    t+= dt;

    if (speed > speed_max)
    {
      speed_max = speed;
    }

    timer.delay_ms(dt);
  }

  terminal << "\n\n";
  terminal << "speed_max = " << speed_max << "\n";

  motor_controll.left_set(0.0);


  while (1)
  {
    __asm("nop");
  }
}



void position_controll()
{
  float p = 0.055;
  float i = -0.01;
  float d = -0.002; 
 
  float k1 = p;
  float k2 = -p + i;
  float k3 = d;

  
  unsigned int step = 0;
  while (1)
  {
    float required_position = 0;

    switch(step)
    { 
      case 0: required_position = ENCODER_DRIVER_WHEEL_CIRCUMFERENCE/4; break;
      case 1: required_position = 0; break;
      case 2: required_position = -ENCODER_DRIVER_WHEEL_CIRCUMFERENCE/4; break;
      case 3: required_position = 0; break;
    }
 
    for (unsigned int i = 0; i < 200; i++) 
    {
      float position = encoder_driver.get_left();
      float speed    = encoder_driver.get_left_speed();

      float u = k1*required_position + k2*position + k3*speed;

      motor_driver.left_set(u*MOTOR_PWM_MAX);

      timer.delay_ms(2);
    }

    step = (step+1)%4;
  }
}


void identification(unsigned int total_steps)
{

  float brace = 78;


  float values[] = {0.0, -0.2, -0.3, -0.35, -0.4, -0.45, 0.2, 0.3, 0.35, 0.4, 0.45};

  float ul = 0.0;
  float ur = 0.0; 

  for (unsigned int step = 0; step < total_steps; step++)
  {
    if ((step%50) == 0)
    {
      ul = values[rand()%11];
      ur = values[rand()%11];
    }

    auto left_speed     = encoder_driver.get_left_speed();
    auto right_speed    = encoder_driver.get_right_speed();

    auto left_position  = encoder_driver.get_left();
    auto right_position = encoder_driver.get_right();

    auto speed          = (left_speed + right_speed)/2.0;
    auto angular_rate   = (right_speed - left_speed)/brace;
    auto angle          = (right_position - left_position)/brace;

    terminal << step << ", " << timer.get_time() << ", " << ul << ", " << ur << ", " ;
    terminal << left_speed << ", " << right_speed << ", ";
    terminal << left_position << ", " << left_position << ", ";
    terminal << speed << ", " << angular_rate << ", " << angle << "\n";

    timer.delay_ms(4);

    motor_driver.left_set(ul*MOTOR_PWM_MAX);
    motor_driver.right_set(ur*MOTOR_PWM_MAX);
  }

  motor_driver.left_set(0);
  motor_driver.left_set(0);
}


        
int main(void) 
{
  SetSysClock(SysClok216_8HSE);

  Gpio<LED_GPIO, LED_PIN, GPIO_MODE_OUT> led;        //user led
  led = 1; 

  low_level_drivers.init(); 

  terminal << "machine ready\n\n";
  
  //Gpio<KEY_GPIO, KEY_PIN, GPIO_MODE_IN_PULLUP> key;  //user button
  //Gpio<TGPIOE, 14, GPIO_MODE_OUT> sensor_led;        //sensor white led

  timer.delay_ms(1000);
  
  identification(2000);

  while (1)
  {
    led = 1; 
    timer.delay_ms(100);

    led = 0; 
    timer.delay_ms(100); 
  }

  return 0;
} 

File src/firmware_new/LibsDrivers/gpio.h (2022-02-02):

#ifndef _GPIO_H_
#define _GPIO_H_


#include <device.h>


#define TGPIOA    ((unsigned char)0)
#define TGPIOB    ((unsigned char)1)
#define TGPIOC    ((unsigned char)2)
#define TGPIOD    ((unsigned char)3)
#define TGPIOE    ((unsigned char)4)
#define TGPIOF    ((unsigned char)5)
#define TGPIOG    ((unsigned char)6)
#define TGPIOH    ((unsigned char)7)
#define TGPIOI    ((unsigned char)8)
#define TGPIOJ    ((unsigned char)9)


#define GPIO_MODE_OUT             0       //push-pull output mode
#define GPIO_MODE_IN_FLOATING     1       //input mode
#define GPIO_MODE_IN_PULLUP       2       //input mode with pullup
#define GPIO_MODE_AN              4       //analog input
#define GPIO_MODE_AF              5       //alternate function
#define GPIO_MODE_OUT_OD          6       //open-drain output mode


template <const unsigned char gpio, unsigned char pin, unsigned char mode = GPIO_MODE_OUT> 
class Gpio
{
  private:
    GPIO_TypeDef *GPIOx;

  public:
    Gpio()
    {
      init();
    }

    void init()
    {
      #ifdef RCC_AHB1ENR_GPIOAEN
      RCC->AHB1ENR|= RCC_AHB1ENR_GPIOAEN;
      #endif

      #ifdef RCC_AHB1ENR_GPIOBEN
      RCC->AHB1ENR|= RCC_AHB1ENR_GPIOBEN;
      #endif

      #ifdef RCC_AHB1ENR_GPIOCEN
      RCC->AHB1ENR|= RCC_AHB1ENR_GPIOCEN;
      #endif

      #ifdef RCC_AHB1ENR_GPIODEN
      RCC->AHB1ENR|= RCC_AHB1ENR_GPIODEN;
      #endif

      #ifdef RCC_AHB1ENR_GPIOEEN
      RCC->AHB1ENR|= RCC_AHB1ENR_GPIOEEN;
      #endif

      #ifdef RCC_AHB1ENR_GPIOFEN
      RCC->AHB1ENR|= RCC_AHB1ENR_GPIOFEN;
      #endif

      #ifdef RCC_AHB1ENR_GPIOGEN
      RCC->AHB1ENR|= RCC_AHB1ENR_GPIOGEN;
      #endif

      #ifdef RCC_AHB1ENR_GPIOHEN
      RCC->AHB1ENR|= RCC_AHB1ENR_GPIOHEN;
      #endif

      #ifdef RCC_AHB1ENR_GPIOIEN
      RCC->AHB1ENR|= RCC_AHB1ENR_GPIOIEN;
      #endif

      #ifdef RCC_AHB1ENR_GPIOJEN
      RCC->AHB1ENR|= RCC_AHB1ENR_GPIOJEN;
      #endif

 


      #ifdef RCC_AHBENR_GPIOAEN
      RCC->AHBENR|= RCC_AHBENR_GPIOAEN;
      #endif

      #ifdef RCC_AHBENR_GPIOBEN
      RCC->AHBENR|= RCC_AHBENR_GPIOBEN;
      #endif

      #ifdef RCC_AHBENR_GPIOCEN
      RCC->AHBENR|= RCC_AHBENR_GPIOCEN;
      #endif

      #ifdef RCC_AHBENR_GPIODEN
      RCC->AHBENR|= RCC_AHBENR_GPIODEN;
      #endif

      #ifdef RCC_AHBENR_GPIOEEN
      RCC->AHBENR|= RCC_AHBENR_GPIOEEN;
      #endif

      #ifdef RCC_AHBENR_GPIODEN
      RCC->AHBENR|= RCC_AHBENR_GPIODEN;
      #endif

      #ifdef RCC_AHBENR_GPIOGEN
      RCC->AHBENR|= RCC_AHBENR_GPIOGEN;
      #endif

      #ifdef RCC_AHBENR_GPIOHEN
      RCC->AHBENR|= RCC_AHBENR_GPIOHEN;
      #endif
      
     




      #ifdef GPIOA
      if (gpio == TGPIOA)
        GPIOx = GPIOA;
      #endif

      #ifdef GPIOB
      if (gpio == TGPIOB)
        GPIOx = GPIOB;
      #endif

      #ifdef GPIOC
      if (gpio == TGPIOC)
        GPIOx = GPIOC;
      #endif

      #ifdef GPIOD
      if (gpio == TGPIOD)
        GPIOx = GPIOD;
      #endif
 
      #ifdef GPIOE
      if (gpio == TGPIOE)
        GPIOx = GPIOE;
      #endif

      #ifdef GPIOF
      if (gpio == TGPIOF)
        GPIOx = GPIOF;
      #endif

      #ifdef GPIOG
      if (gpio == TGPIOG)
        GPIOx = GPIOG;
      #endif

      #ifdef GPIOH
      if (gpio == TGPIOH)
        GPIOx = GPIOH;
      #endif

      #ifdef GPIOI
      if (gpio == TGPIOI)
        GPIOx = GPIOI;
      #endif

      #ifdef GPIOJ
      if (gpio == TGPIOJ)
        GPIOx = GPIOJ;
      #endif 

      set_mode(mode);
    } 

    inline void set_mode(const unsigned char pin_mode)
       {
         if (pin_mode == GPIO_MODE_OUT)
         {
           //gpio speed 50MHz
           GPIOx->OSPEEDR &= ~(GPIO_OSPEEDER_OSPEEDR0 << (pin * 2));
           GPIOx->OSPEEDR |= ((uint32_t)(0x03) << (pin * 2));

           //push-pull output
           GPIOx->OTYPER &= ~((GPIO_OTYPER_OT_0) << ((uint16_t)pin));
           GPIOx->OTYPER |= (uint16_t)(((uint16_t)0x00) << ((uint16_t)pin));

           //pin as output
           GPIOx->MODER  &= ~(GPIO_MODER_MODER0 << (pin * 2));
           GPIOx->MODER |= (((uint32_t)0x01) << (pin * 2));
         }

         //input mode, no pull-up
         if (pin_mode == GPIO_MODE_IN_FLOATING)
         {
           //gpio speed 50MHz
           GPIOx->OSPEEDR &= ~(GPIO_OSPEEDER_OSPEEDR0 << (pin * 2));
           GPIOx->OSPEEDR |= ((uint32_t)(0x03) << (pin * 2));

           //pin as output
           GPIOx->MODER  &= ~(GPIO_MODER_MODER0 << (pin * 2));
           GPIOx->MODER |= (((uint32_t)0x00) << (pin * 2));
         }

         //input mode, pull-up
         if (pin_mode == GPIO_MODE_IN_PULLUP)
         {
           //gpio speed 50MHz
           GPIOx->OSPEEDR &= ~(GPIO_OSPEEDER_OSPEEDR0 << (pin * 2));
           GPIOx->OSPEEDR |= ((uint32_t)(0x03) << (pin * 2));

           //pin as output
           GPIOx->MODER  &= ~(GPIO_MODER_MODER0 << (pin * 2));
           GPIOx->MODER |= (((uint32_t)0x00) << (pin * 2));
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

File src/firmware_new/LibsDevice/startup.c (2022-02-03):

#ifdef __cplusplus
extern "C" {
#endif

#include <stdint.h>

// Memory locations defined by the linker
extern uint32_t _estack[];
extern uint32_t _sdata[], _edata[];
extern uint32_t _etext[];                // End of code/flash
extern void (*__init_array_start)();     //constructors
extern void (*__init_array_end)();

extern int main(void);

// Default interrupt handler
void __attribute__((interrupt("IRQ"))) Default_Handler()
{
    while (1)
    {

    }
}

void Reset_Handler()                    __attribute__((naked, aligned(2)));
/* Weak definitions of handlers point to Default_Handler if not implemented */
void NMI_Handler()                      __attribute__ ((weak, alias("Default_Handler")));
void HardFault_Handler()                __attribute__ ((weak, alias("Default_Handler")));
void MemManage_Handler()                __attribute__ ((weak, alias("Default_Handler")));
void BusFault_Handler()                 __attribute__ ((weak, alias("Default_Handler")));
void UsageFault_Handler()               __attribute__ ((weak, alias("Default_Handler")));
void DebugMon_Handler()                 __attribute__ ((weak, alias("Default_Handler")));
void PendSV_Handler()                   __attribute__ ((weak, alias("Default_Handler")));
void SVC_Handler()                      __attribute__ ((weak, alias("Default_Handler")));
void SysTick_Handler()                  __attribute__ ((weak, alias("Default_Handler")));


void WWDG_IRQHandler()                  __attribute__((weak, alias("Default_Handler")));        /* Window WatchDog */
void PVD_IRQHandler()                   __attribute__((weak, alias("Default_Handler")));        /* PVD through EXTI Line detection */
void TAMP_STAMP_IRQHandler()            __attribute__((weak, alias("Default_Handler")));        /* Tamper and TimeStamps through the EXTI line */
void RTC_WKUP_IRQHandler()              __attribute__((weak, alias("Default_Handler")));        /* RTC Wakeup through the EXTI line */
void FLASH_IRQHandler()                 __attribute__((weak, alias("Default_Handler")));        /* FLASH */
void RCC_IRQHandler()                   __attribute__((weak, alias("Default_Handler")));        /* RCC */
void EXTI0_IRQHandler()                 __attribute__((weak, alias("Default_Handler")));        /* EXTI Line0 */
void EXTI1_IRQHandler()                 __attribute__((weak, alias("Default_Handler")));        /* EXTI Line1 */
void EXTI2_IRQHandler()                 __attribute__((weak, alias("Default_Handler")));        /* EXTI Line2 */
void EXTI3_IRQHandler()                 __attribute__((weak, alias("Default_Handler")));        /* EXTI Line3 */
void EXTI4_IRQHandler()                 __attribute__((weak, alias("Default_Handler")));        /* EXTI Line4 */
void DMA1_Stream0_IRQHandler()          __attribute__((weak, alias("Default_Handler")));        /* DMA1 Stream 0 */
void DMA1_Stream1_IRQHandler()          __attribute__((weak, alias("Default_Handler")));        /* DMA1 Stream 1 */
void DMA1_Stream2_IRQHandler()          __attribute__((weak, alias("Default_Handler")));        /* DMA1 Stream 2 */
void DMA1_Stream3_IRQHandler()          __attribute__((weak, alias("Default_Handler")));        /* DMA1 Stream 3 */
void DMA1_Stream4_IRQHandler()          __attribute__((weak, alias("Default_Handler")));        /* DMA1 Stream 4 */
void DMA1_Stream5_IRQHandler()          __attribute__((weak, alias("Default_Handler")));        /* DMA1 Stream 5 */
void DMA1_Stream6_IRQHandler()          __attribute__((weak, alias("Default_Handler")));        /* DMA1 Stream 6 */
void ADC_IRQHandler()                   __attribute__((weak, alias("Default_Handler")));        /* ADC1, ADC2 and ADC3s */
void CAN1_TX_IRQHandler()               __attribute__((weak, alias("Default_Handler")));        /* CAN1 TX */
void CAN1_RX0_IRQHandler()              __attribute__((weak, alias("Default_Handler")));        /* CAN1 RX0 */
void CAN1_RX1_IRQHandler()              __attribute__((weak, alias("Default_Handler")));        /* CAN1 RX1 */
void CAN1_SCE_IRQHandler()              __attribute__((weak, alias("Default_Handler")));        /* CAN1 SCE */
void EXTI9_5_IRQHandler()               __attribute__((weak, alias("Default_Handler")));        /* External Line[9:5]s */
void TIM1_BRK_TIM9_IRQHandler()         __attribute__((weak, alias("Default_Handler")));        /* TIM1 Break and TIM9 */
void TIM1_UP_TIM10_IRQHandler()         __attribute__((weak, alias("Default_Handler")));        /* TIM1 Update and TIM10 */
void TIM1_TRG_COM_TIM11_IRQHandler()    __attribute__((weak, alias("Default_Handler")));        /* TIM1 Trigger and Commutation and TIM11 */
void TIM1_CC_IRQHandler()               __attribute__((weak, alias("Default_Handler")));        /* TIM1 Capture Compare */
void TIM2_IRQHandler()                  __attribute__((weak, alias("Default_Handler")));        /* TIM2 */
void TIM3_IRQHandler()                  __attribute__((weak, alias("Default_Handler")));        /* TIM3 */
void TIM4_IRQHandler()                  __attribute__((weak, alias("Default_Handler")));        /* TIM4 */
void I2C1_EV_IRQHandler()               __attribute__((weak, alias("Default_Handler")));        /* I2C1 Event */
void I2C1_ER_IRQHandler()               __attribute__((weak, alias("Default_Handler")));        /* I2C1 Error */
void I2C2_EV_IRQHandler()               __attribute__((weak, alias("Default_Handler")));        /* I2C2 Event */
void I2C2_ER_IRQHandler()               __attribute__((weak, alias("Default_Handler")));        /* I2C2 Error */
void SPI1_IRQHandler()                  __attribute__((weak, alias("Default_Handler")));        /* SPI1 */
void SPI2_IRQHandler()                  __attribute__((weak, alias("Default_Handler")));        /* SPI2 */
void USART1_IRQHandler()                __attribute__((weak, alias("Default_Handler")));        /* USART1 */
void USART2_IRQHandler()                __attribute__((weak, alias("Default_Handler")));        /* USART2 */
void USART3_IRQHandler()                __attribute__((weak, alias("Default_Handler")));        /* USART3 */
void EXTI15_10_IRQHandler()             __attribute__((weak, alias("Default_Handler")));        /* External Line[15:10]s */
void RTC_Alarm_IRQHandler()             __attribute__((weak, alias("Default_Handler")));        /* RTC Alarm (A and B) through EXTI Line */
void OTG_FS_WKUP_IRQHandler()           __attribute__((weak, alias("Default_Handler")));        /* USB OTG FS Wakeup through EXTI line */
void TIM8_BRK_TIM12_IRQHandler()        __attribute__((weak, alias("Default_Handler")));        /* TIM8 Break and TIM12 */
void TIM8_UP_TIM13_IRQHandler()         __attribute__((weak, alias("Default_Handler")));        /* TIM8 Update and TIM13 */
void TIM8_TRG_COM_TIM14_IRQHandler()    __attribute__((weak, alias("Default_Handler")));        /* TIM8 Trigger and Commutation and TIM14 */
void TIM8_CC_IRQHandler()               __attribute__((weak, alias("Default_Handler")));        /* TIM8 Capture Compare */
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

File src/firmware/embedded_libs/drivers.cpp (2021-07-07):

#include <drivers.h>

Drivers drivers;

Terminal                  terminal;
Timer                     timer;
TI2C<TGPIOD, 1, 2, 50>    i2c;
IMU                       imu_sensor;
ADC_driver                adc;
LineSensor                line_sensor;
DistanceSensor            distance_sensor;
EncoderSensor             encoder_sensor;
MotorControll             motor_controll;
Key                       key;

Drivers::Drivers()
{

}

Drivers::~Drivers()
{

}

int Drivers::init()
{
  led = 1;

  terminal.init();
  terminal << "\n\n\n#####\n\n\n";
  terminal << "terminal init [DONE]\n"; 

  terminal << "initializing memory ";
  unsigned int mem_res = mem_init();
  terminal << "[DONE], heap start at " << mem_res << "\n"; 

  terminal << "initializing timer ";
  timer.init();
  timer.delay_ms(20);
  terminal << "[DONE]\n";

  terminal << "initializing i2c ";
  i2c.init();
  terminal << "[DONE]\n";

  terminal << "initializing IMU ";
  imu_sensor.init(i2c);
  terminal << " [DONE] with result " << imu_sensor.present() << "\n";


  terminal << "initializing adc ";
  adc.init();
  terminal << "[DONE]\n"; 

  terminal << "initializing line_sensor ";
  line_sensor.init();
  terminal << "[DONE]\n";

  terminal << "initializing distance_sensor ";
  distance_sensor.init();
  terminal << "[DONE]\n";

  terminal << "initializing encoder_sensor ";
  encoder_sensor.init();
  terminal << "[DONE]\n";

  terminal << "initializing motor_controll ";
  motor_controll.init();
  terminal << "[DONE]\n";

  terminal << "initializing key ";
  key.init();
  terminal << "[DONE]\n";

  terminal << "cpu speed set to " << F_CPU/1000000 << " MHz\n";

  terminal << "\n\n";
  terminal << "initializing sequence done\n\n";
  terminal << "motoko uprising ready\n\n";
 
  led = 0; 

  return 0;
}




void Drivers::test_imu_sensor(int count)
{
  terminal << "\test_imu_sensor\n";

  bool run = true;
  while (run)
  {
    if (imu_sensor.ready())
    {
        if (count > 0)
          count--;
        if (count == 0)
          run = false;

        led = 1;

        terminal << imu_sensor.angular_rate.x << " ";
        terminal << imu_sensor.angular_rate.y << " ";
        terminal << imu_sensor.angular_rate.z << " ";

        terminal << " : ";

        terminal << imu_sensor.acceleration.x << " ";
        terminal << imu_sensor.acceleration.y << " ";
        terminal << imu_sensor.acceleration.z << " ";

        terminal << " : ";

        terminal << imu_sensor.angle.x << " ";
        terminal << imu_sensor.angle.y << " ";
        terminal << imu_sensor.angle.z << " ";

        terminal << "\n";

        led = 0;

        timer.delay_ms(200);
    }
  }
}


void Drivers::test_line_sensor(int count)
{
  terminal << "\ntest_line_sensor\n";

  bool run = true;

  line_sensor.on();
  while (run)
  {
    if (line_sensor.ready())
    {
        if (count > 0)
          count--;
        if (count == 0)
          run = false;

        led = 1; 

        terminal << line_sensor.result.on_line_count << " ";
        terminal << line_sensor.result.line_type << " ";
        terminal << line_sensor.result.line_lost_type << " ";
        terminal << line_sensor.result.center_line_position << " ";

        terminal << "\n";

        led = 0;

        timer.delay_ms(200);
    }
  }
  line_sensor.off();
}

void Drivers::test_ir_sensor(int count)
{
    terminal << "\ntest_ir_sensor\n";

    bool run = true;

    Array<int, LINE_SENSOR_COUNT> result;


    line_sensor.on();
    while (run)
    {
        if (line_sensor.ready())
        {
            result = line_sensor.adc_result;

            if (count > 0)
                count--;
            if (count == 0)
                run = false;

            led = 1;

            for (unsigned int i = 0; i < result.size(); i++)
            {
                terminal << result[i] << " ";
            }

            terminal << "\n";

            led = 0;

            timer.delay_ms(200);
      }
    }
    line_sensor.off();
}


void Drivers::test_distance_sensor(int count)
{
  terminal << "\test_distance_sensor\n";

  bool run = true;
  while (run)
  {
    if (distance_sensor.ready())
    {
        if (count > 0)
          count--;
        if (count == 0)
          run = false;

        led = 1;

        distance_sensor.print();

        led = 0;

        timer.delay_ms(200);
    }
  }
}


void Drivers::test_encoder_sensor(int count)
{
  terminal << "\ntest_encoder_sensor\n";

  bool run = true;
  while (run)
  {
        if (count > 0)
          count--;
        if (count == 0)
          run = false;

        led = 1;

        terminal << encoder_sensor.get_left() << " ";
        terminal << encoder_sensor.get_right() << " ";
        terminal << encoder_sensor.get_distance() << " ";

        terminal << "\n";

        led = 0;

        timer.delay_ms(200);
  }
}


void Drivers::test_motor_speed_feedback()
{
  terminal << "\ntest_motor_speed_feedback\n";

  unsigned int cnt = 0;
  float required_left = 0;
  float required_right = 0;

  while (1)
  {
    led = 1;

    motor_controll.set_left_speed(required_left);
    motor_controll.set_right_speed(required_right);

    terminal << required_left << " " << motor_controll.get_left_speed() << " ";
    terminal << required_right << " " << motor_controll.get_right_speed() << "\n";

    led = 0;

    timer.delay_ms(200);

    cnt++;

    switch ((cnt/20)%4)
    {
      case 0: required_left = 0.2; required_right = 0.2; break;
      case 1: required_left = 0.3; required_right = 0.3; break;
      case 2: required_left = 0.5; required_right = 0.5; break;
      case 3: required_left = 0.8; required_right = 0.8; break;
    }
  }
}





void Drivers::test_motor_gyro_feedback()
{
  terminal << "\ntest_motor_gyro_feedback\n";

  PID pid(0.00004, 0.0, 0.0001, 1.0);

  while (1)
  {
    if (imu_sensor.ready())
    {
      led = 1;

      float angle = imu_sensor.angle.z;
      float error = 0.0 - angle;

      float turn = pid.process(error, angle);

      motor_controll.set_left_speed(-turn);
      motor_controll.set_right_speed(turn);

      // terminal << "angle " << angle << "\n";

      led = 0;
    }
  }
}
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

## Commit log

2021-03-14 rl + env for line follower
    [0.obj, 0.urdf, 1.obj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]
2021-03-19 model updated
    [forward_chassis.stl, model.stl, motoko_chassis.stl]
2021-03-24 motor driver, some bugs fixed
    [adc_driver.cpp, adc_driver.h, device_config.h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]

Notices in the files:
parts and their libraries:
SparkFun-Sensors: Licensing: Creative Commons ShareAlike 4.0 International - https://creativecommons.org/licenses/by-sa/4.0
